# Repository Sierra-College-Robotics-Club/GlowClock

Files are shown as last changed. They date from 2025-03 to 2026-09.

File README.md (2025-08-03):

# GlowClock

This is a project from Sierra College Robotics Club, A glow-in-the-dark display, activated by UV LEDs scanning over a glow-in-the-dark surface. It displays messages, the time, and features various patterns and simple games! 

See [The Schematic](GlowClockPCB/Docs/GlowClockSchematicPrint.pdf) and [The Code](code/glowClock.py) to get started working with it.

The GlowClock design evolved from our previous project, the Whiteboard Clock, but with the goals of being more mechanically reliable, while showing a new and unique way of using technology we're all familar with: Glow in the dark materials!

The GlowClock is a collaborative effort by the Robotics Club, featuring PCB design and software by Patrick Leiser, with mechanical design and assembly contributions from many talented club members.

## In the media
We presented the GlowClock at OpenSauce 2025, and were featured in [This Video](https://youtu.be/PQWQQJ_izac?t=115) by Jeff Geerling. We also posted some media on [our instagram](https://www.instagram.com/p/DJci4YWBg5E/)

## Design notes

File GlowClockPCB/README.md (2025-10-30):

# GlowClock PCB
This PCB was designed to, in addition to supporting the glowclock, be a modular prototyping board for various other projects as well, with all unused GPIO broken out and accessible.

V1.0 boards have been produced and are in active use, V1.1 boards are currently under development.

## Errata
### V1.0
- The second motor-driver board slot (A2) is not fully populated with the required control signals
- The Raspberry Pi 40 pin header (not to be confused with the Pi Pico's socket) has 0.2mm hole spacing instead of the traditional 2.54mm spacing
- The i2c SDA pin for the I2C_LCD connector is connected to GPIO22 instead of GPIO20. This can be resolved by cutting the trace and green-wiring to the Pi Pico pin 26.

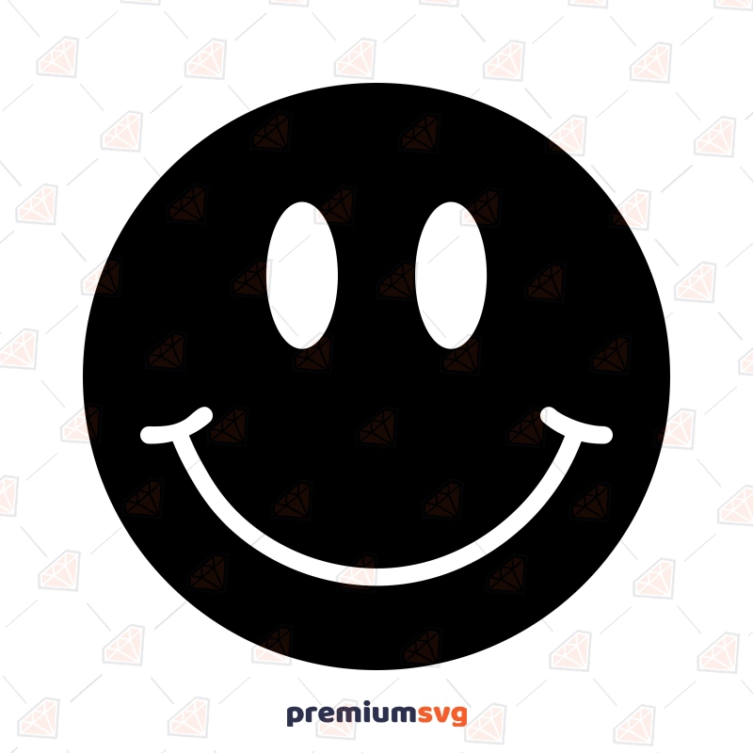
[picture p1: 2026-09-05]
code/images/smile-inv.webp

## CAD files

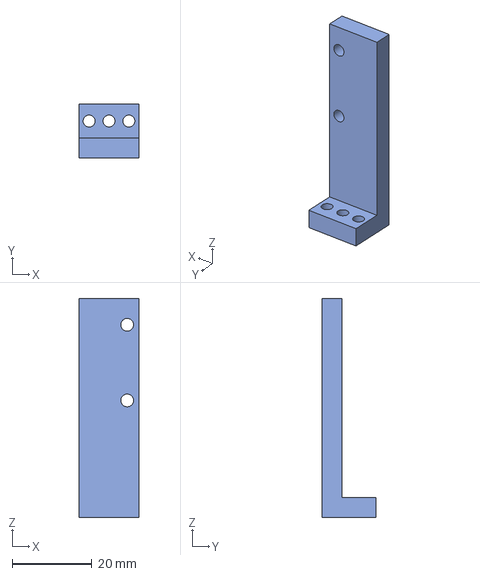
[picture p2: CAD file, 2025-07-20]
3d Models/GlowClockOriginSwitchBracket-2.step
15.0 x 13.5 x 55.0 mm

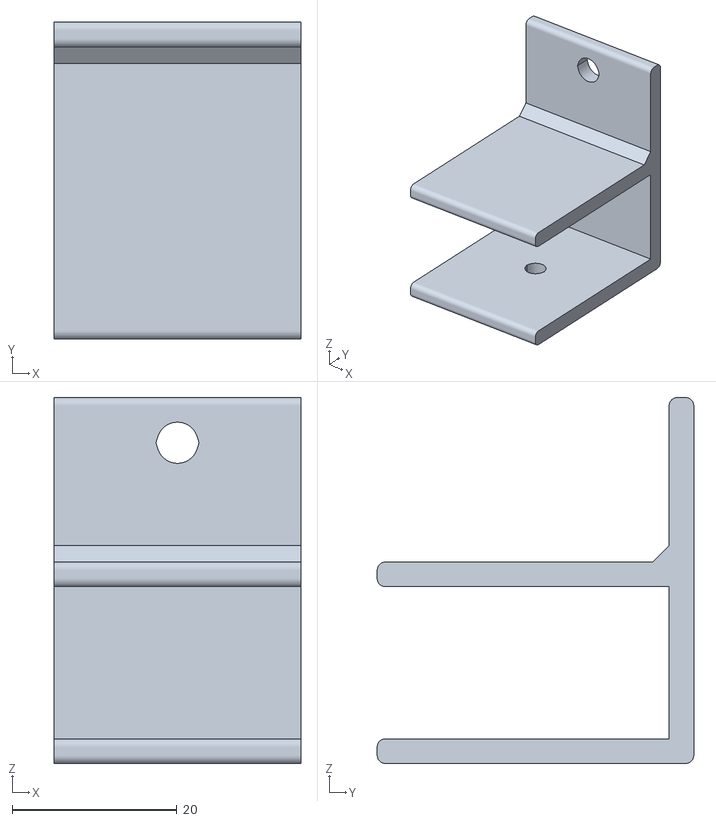
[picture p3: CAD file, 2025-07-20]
3d Models/GraphBot/GraphBotBracket.stl
30.0 x 38.5 x 44.5

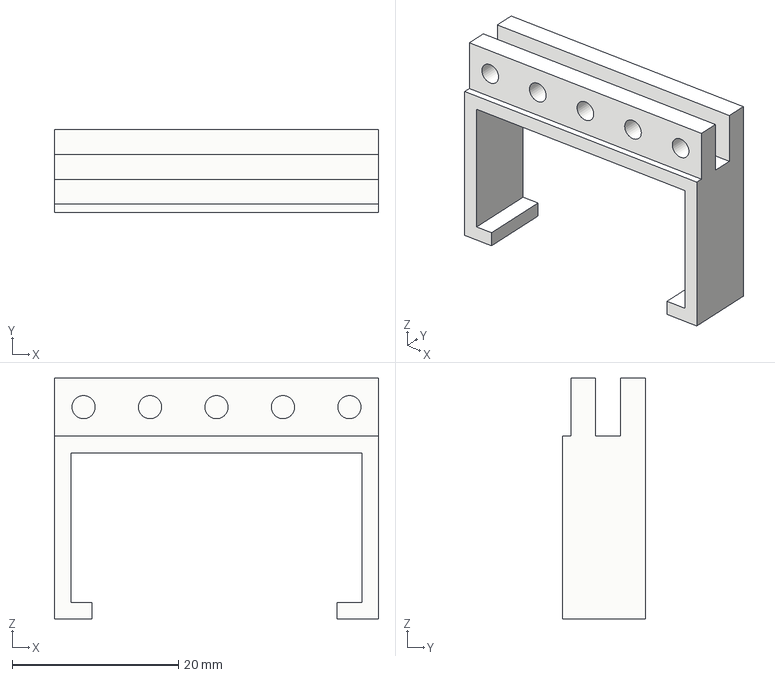
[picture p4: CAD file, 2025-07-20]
3d Models/Belt_Mesh_Joint v3.3mf
39.0 x 10.0 x 29.0 mm

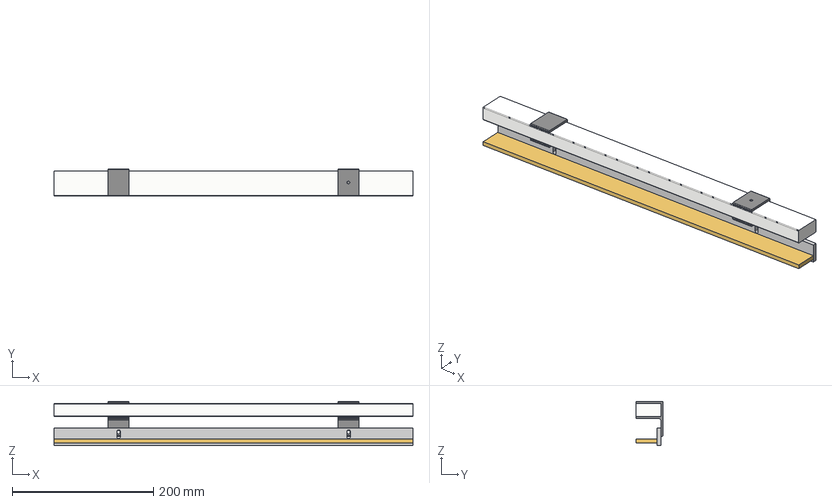
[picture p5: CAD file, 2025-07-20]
3d Models/GraphBot/GraphBotMount.step
508.2 x 38.5 x 62.9 mm
Mount
WoodBracket
LedStripHolder
Mount(Mirror)

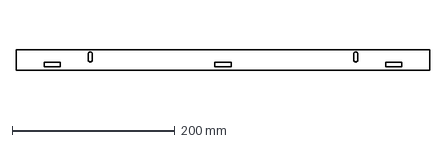
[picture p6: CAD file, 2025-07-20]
3d Models/GraphBot/WoodBracketCutout.dxf
508.0 x 25.0 mm

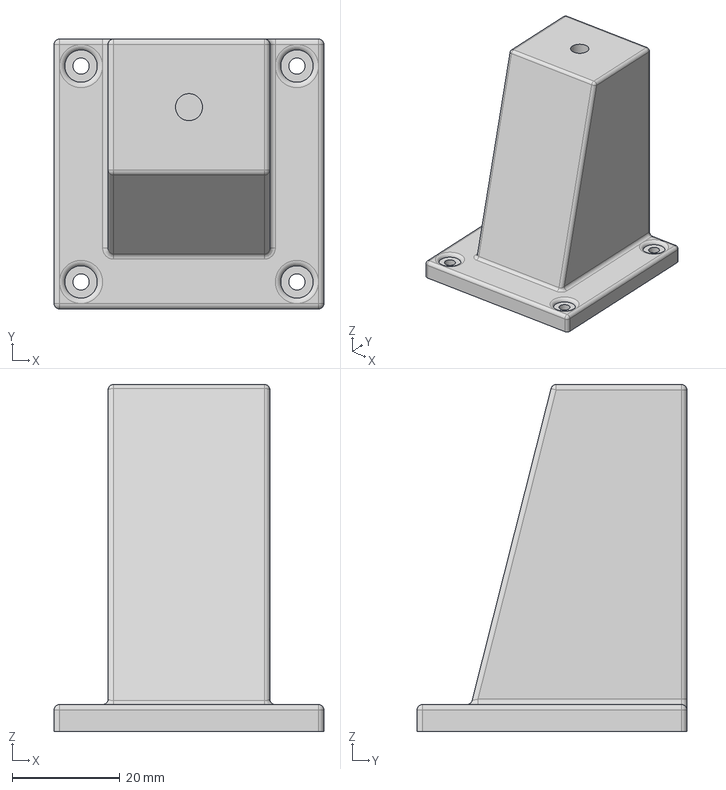
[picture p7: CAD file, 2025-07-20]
3d Models/GraphBot/MotorTensionMount v1.step
50.0 x 50.0 x 64.3 mm

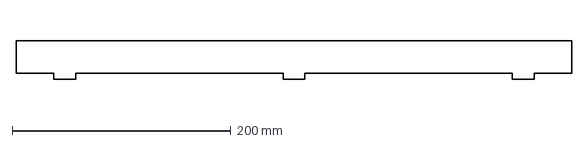
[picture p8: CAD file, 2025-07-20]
3d Models/GraphBot/LedMountCutout.dxf
508.0 x 35.5 mm

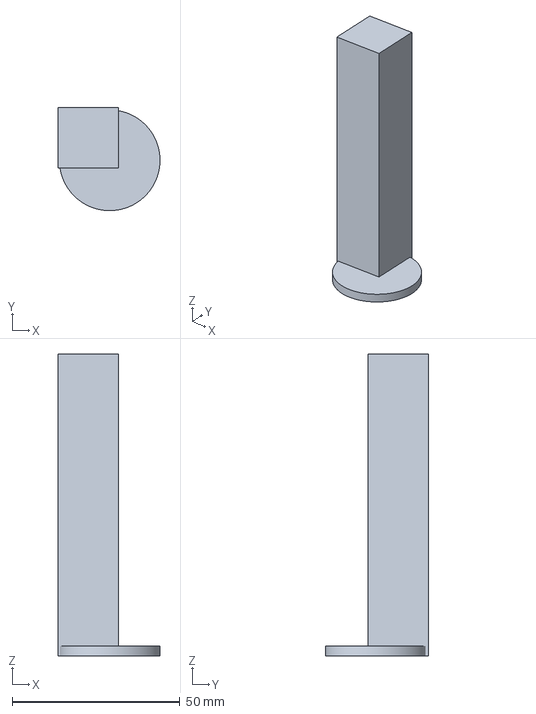
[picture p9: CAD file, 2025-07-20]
3d Models/shortenedactually3dprintableglowclockmount.3mf
30.4 x 30.8 x 90.0 mm

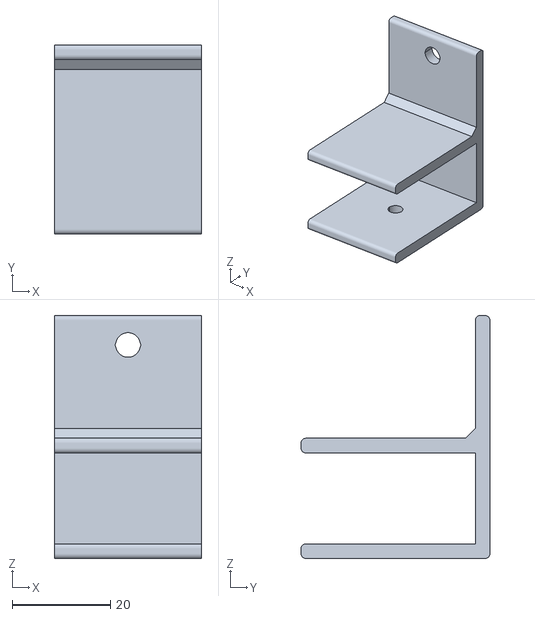
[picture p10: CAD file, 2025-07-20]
3d Models/GraphBot/MountFixv1.stl
30.0 x 38.5 x 49.5

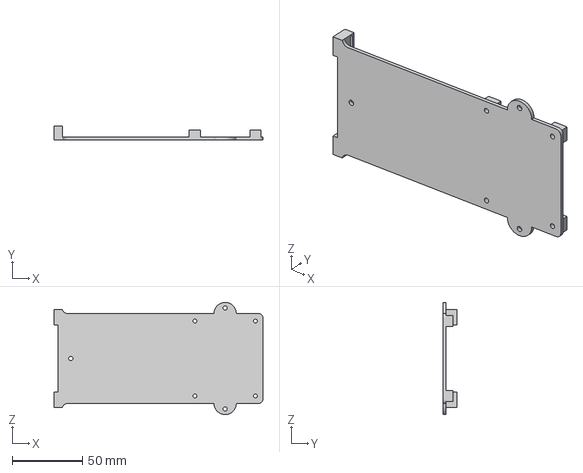
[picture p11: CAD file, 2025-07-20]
3d Models/glow clock pcb mount v2.3mf
149.0 x 10.0 x 80.0 mm

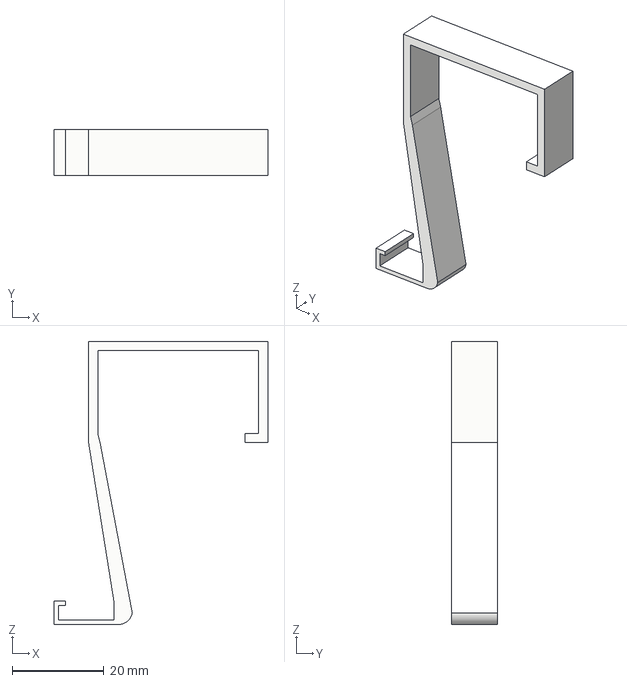
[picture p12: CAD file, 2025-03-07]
3d Models/LED_Strip_Hook v2.step
46.5 x 10.0 x 61.6 mm

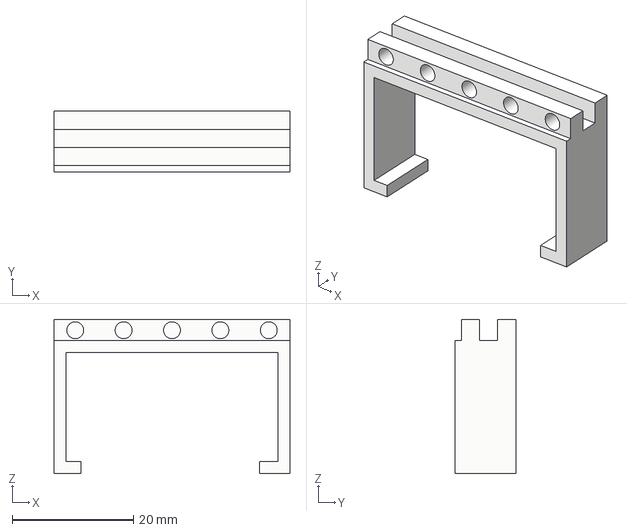
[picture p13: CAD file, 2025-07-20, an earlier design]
3d Models/Belt_Mesh_Joint v2.3mf
39.0 x 10.0 x 25.5 mm

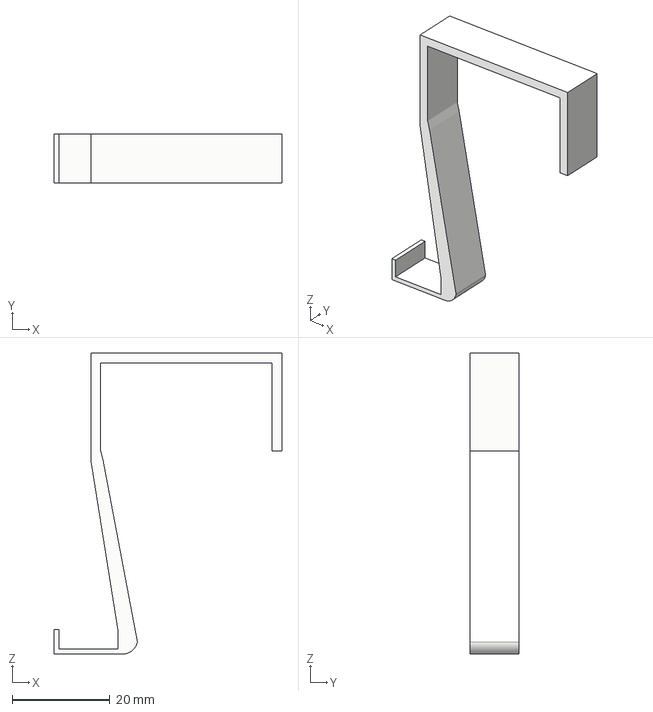
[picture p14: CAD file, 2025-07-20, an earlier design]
3d Models/LED_Strip_Hook v1.3mf
46.5 x 10.0 x 61.5 mm

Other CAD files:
3d Models/GlowClockOriginSwitchBracket.stl
3d Models/GraphBot/Motor Tension Moint.stl
3d Models/PowerSupplyCornerBracket.3mf
3d Models/LED_Strip_Hook v2.3mf
3d Models/PowerSupplyCornerBracket.stl

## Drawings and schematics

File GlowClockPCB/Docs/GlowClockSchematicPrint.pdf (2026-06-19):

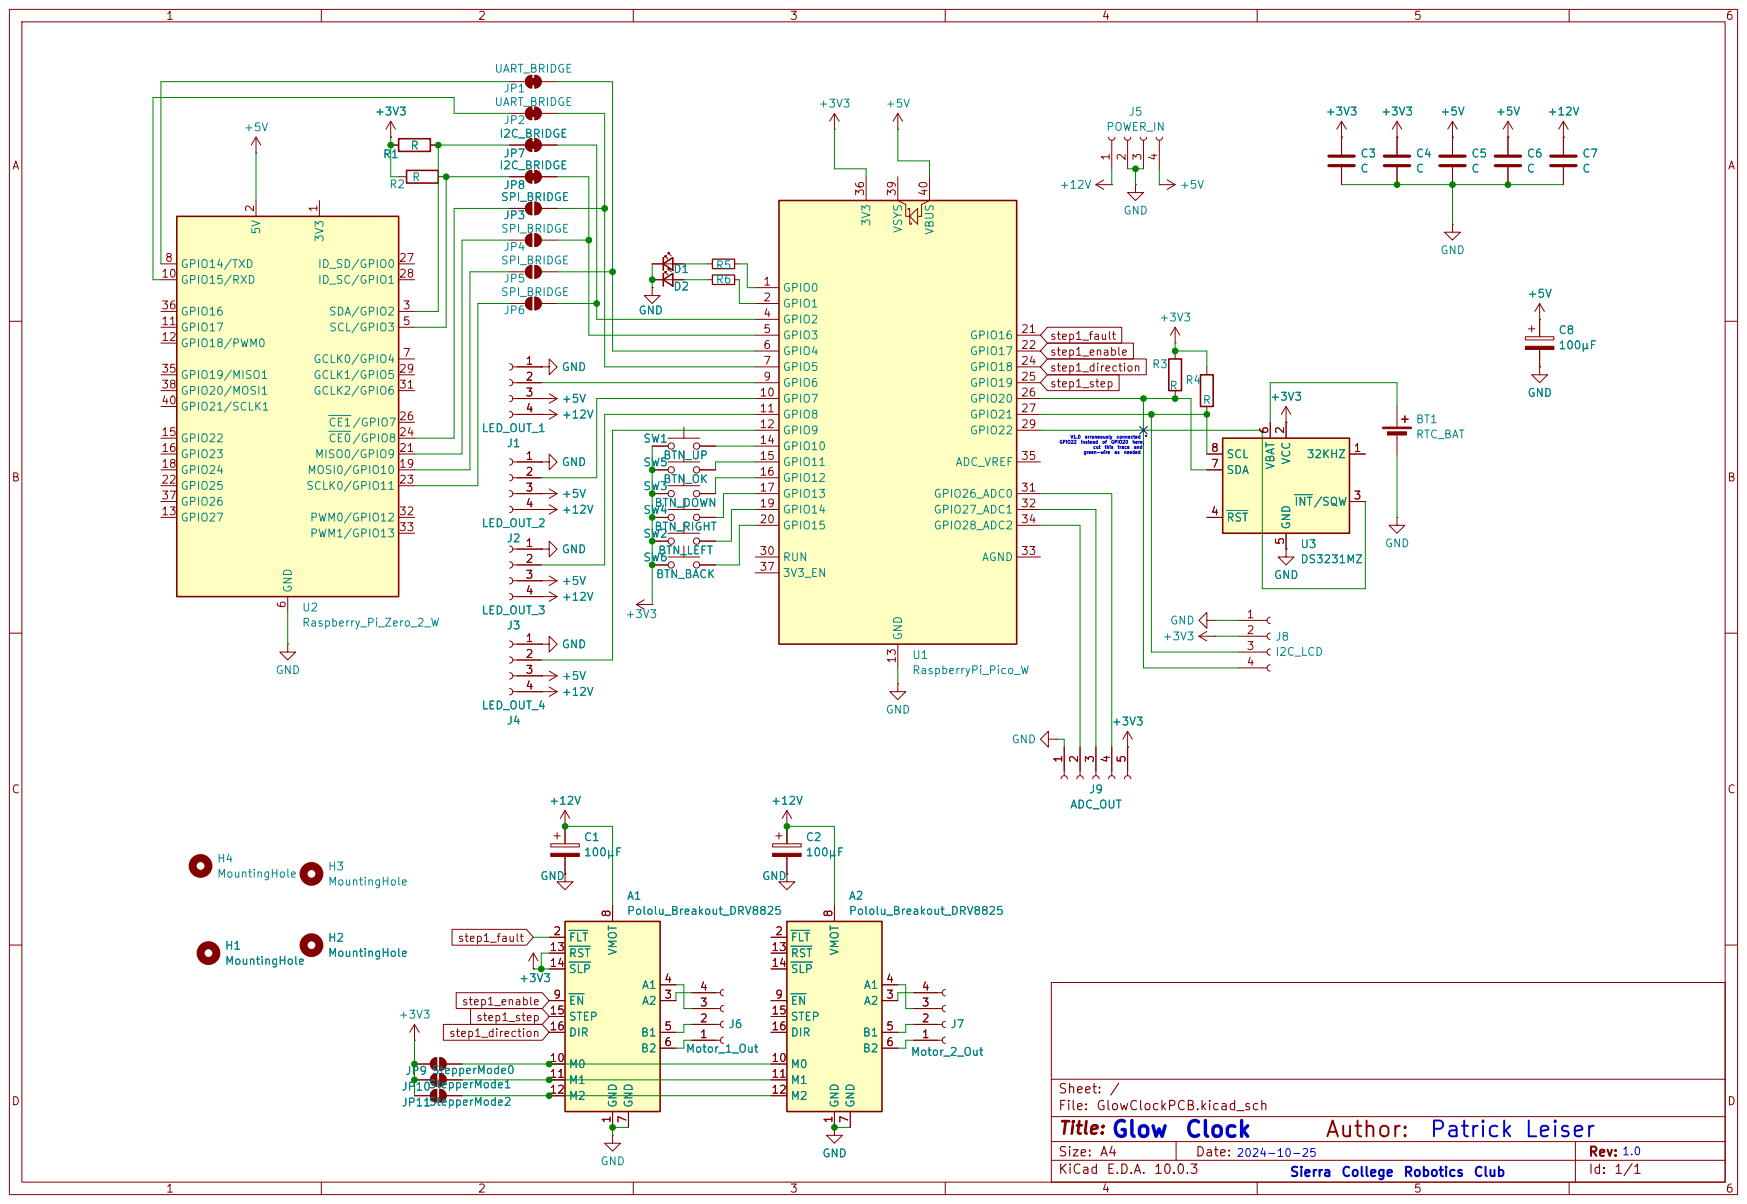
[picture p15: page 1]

Size: A4 | 2024-10-25 Sierra College Robotics Club | Rev: 1.0
KiCad E.D.A. 10.0.3 | | Id: 1/1

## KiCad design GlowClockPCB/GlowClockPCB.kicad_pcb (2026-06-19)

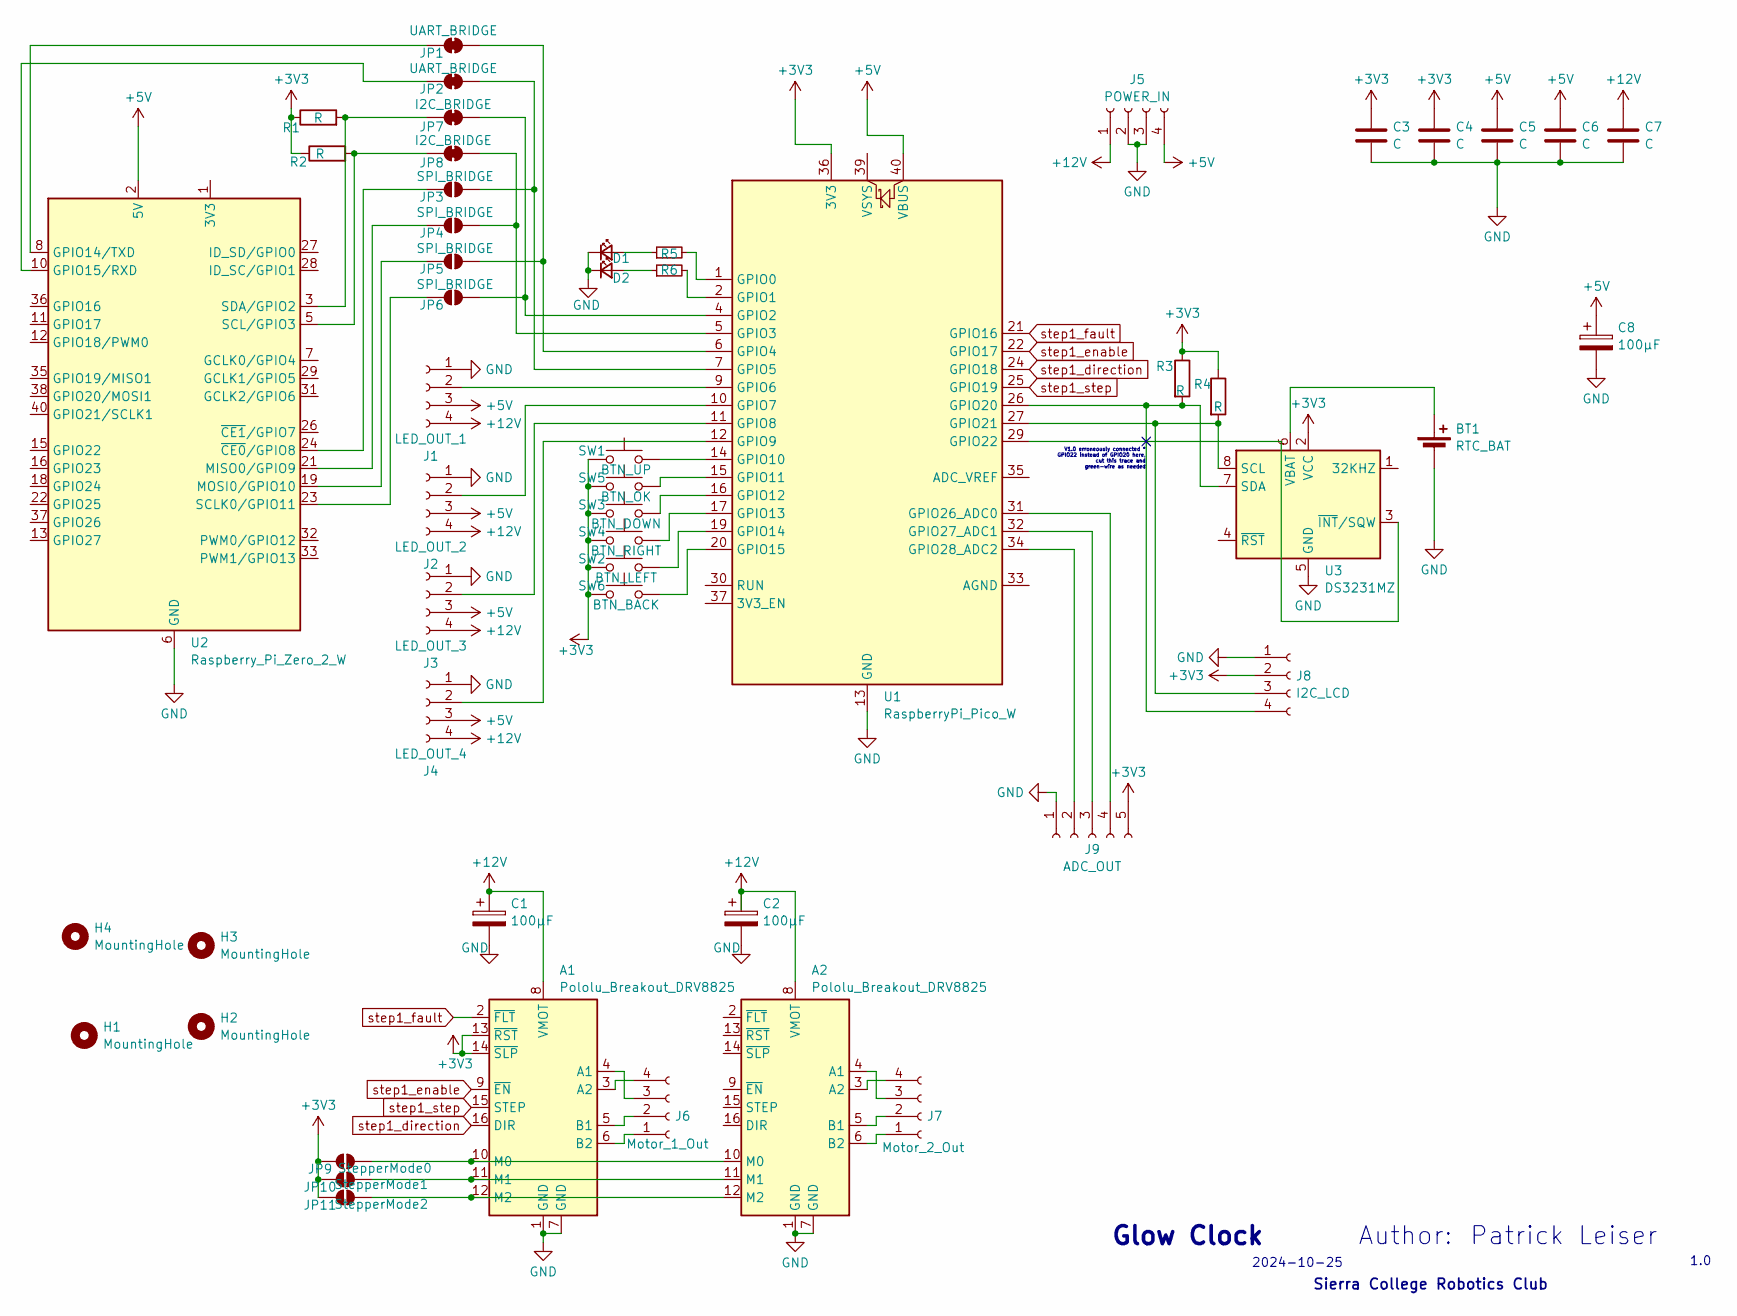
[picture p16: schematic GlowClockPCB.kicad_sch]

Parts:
A1, A2: Pololu_Breakout_DRV8825; Pololu_Breakout-16_15.2x20.3mm
BT1: RTC_BAT; BatteryHolder_LINX_BAT-HLD-012-SMT
C1, C2, C8: 100µF; CP_Radial_D10.0mm_P5.00mm
C3, C4, C5, C6, C7: C; C_0603_1608Metric
D1, D2: LED_Small; LED_0603_1608Metric
H1, H2, H3, H4: MountingHole; MountingHole_3.2mm_M3
J1: LED_OUT_1; JST_XH_B4B-XH-A_1x04_P2.50mm_Vertical
J2: LED_OUT_2; JST_XH_B4B-XH-A_1x04_P2.50mm_Vertical
J3: LED_OUT_3; JST_XH_B4B-XH-A_1x04_P2.50mm_Vertical
J4: LED_OUT_4; JST_XH_B4B-XH-A_1x04_P2.50mm_Vertical
J5: POWER_IN; TE_MATE-N-LOK_350211-1_1x04_P5.08mm_Vertical
J6: Motor_1_Out; JST_XH_B4B-XH-A_1x04_P2.50mm_Vertical
J7: Motor_2_Out; JST_XH_B4B-XH-A_1x04_P2.50mm_Vertical
J8: I2C_LCD; PinHeader_1x04_P2.54mm_Vertical
J9: ADC_OUT; JST_XH_B5B-XH-A_1x05_P2.50mm_Vertical
JP1, JP2: UART_BRIDGE; SolderJumper-2_P1.3mm_Bridged_Pad1.0x1.5mm
JP3, JP4, JP5, JP6: SPI_BRIDGE; SolderJumper-2_P1.3mm_Open_Pad1.0x1.5mm
JP7, JP8: I2C_BRIDGE; SolderJumper-2_P1.3mm_Bridged_Pad1.0x1.5mm
JP9: StepperMode0; SolderJumper-2_P1.3mm_Open_Pad1.0x1.5mm
JP10: StepperMode1; SolderJumper-2_P1.3mm_Open_Pad1.0x1.5mm
JP11: StepperMode2; SolderJumper-2_P1.3mm_Open_Pad1.0x1.5mm
R1, R2, R3, R4: R; R_0603_1608Metric
R5, R6: R_Small; R_0603_1608Metric
SW1: BTN_UP; SW_Push_1P1T_NO_6x6mm_H9.5mm
SW2: BTN_LEFT; SW_Push_1P1T_NO_6x6mm_H9.5mm
SW3: BTN_DOWN; SW_Push_1P1T_NO_6x6mm_H9.5mm
SW4: BTN_RIGHT; SW_Push_1P1T_NO_6x6mm_H9.5mm
SW5: BTN_OK; SW_Push_1P1T_NO_6x6mm_H9.5mm
SW6: BTN_BACK; SW_Push_1P1T_NO_6x6mm_H9.5mm
U1: RaspberryPi_Pico_W; RaspberryPi_Pico_Common
U2: Raspberry_Pi_Zero_2_W; PinHeader_2x20_P2.00mm_Vertical
U3: DS3231MZ; SOIC-8_3.9x4.9mm_P1.27mm

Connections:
+3V3: A1.13 (~RST), A1.14 (~SLP), C3.1, C4.1, J8.2, J9.5, JP9.1 (A), JP10.1 (A), JP11.1 (A), R1.1, R2.1, R3.1, R4.1, SW1.1, SW2.1, SW3.1, SW4.1, SW5.1, SW6.1, U1.36 (3V3), U3.2 (VCC)
+5V: C5.1, C6.1, C8.1, J1.3, J2.3, J3.3, J4.3, J5.4, U1.40 (VBUS), U2.2 (5V), U2.4 (5V)
+12V: A1.8 (VMOT), A2.8 (VMOT), C1.1, C2.1, C7.1, J1.4, J2.4, J3.4, J4.4, J5.1
GND: A1.1 (GND), A1.7 (GND), A2.1 (GND), A2.7 (GND), BT1.2 (-), C1.2, C2.2, C3.2, C4.2, C5.2, C6.2, C7.2, C8.2, D1.1 (K), D2.1 (K), J1.1, J2.1, J3.1, J4.1, J5.2, J5.3, J8.1, J9.1, U1.3 (GND), U1.8 (GND), U1.13 (GND), U1.18 (GND), U1.23 (GND), U1.28 (GND), U1.38 (GND), U2.6 (GND), U2.9 (GND), U2.14 (GND), U2.20 (GND), U2.25 (GND), U2.30 (GND), U2.34 (GND), U2.39 (GND), U3.5 (GND)
unnamed: A1.4 (A1), J6.3
unnamed: A1.3 (A2), J6.4
unnamed: A1.5 (B1), J6.2
unnamed: A1.6 (B2), J6.1
unnamed: A1.10 (M0), A2.10 (M0), JP9.2 (B)
unnamed: A1.11 (M1), A2.11 (M1), JP10.2 (B)
unnamed: A1.12 (M2), A2.12 (M2), JP11.2 (B)
unnamed: A2.4 (A1), J7.3
unnamed: A2.3 (A2), J7.4
unnamed: A2.5 (B1), J7.2
unnamed: A2.6 (B2), J7.1
unnamed: BT1.1 (+), U3.6 (VBAT)
unnamed: D1.2 (A), R5.1
unnamed: D2.2 (A), R6.1
unnamed: J1.2, U1.9 (GPIO6)
unnamed: J2.2, U1.10 (GPIO7)
unnamed: J3.2, U1.11 (GPIO8)
unnamed: J4.2, U1.12 (GPIO9)
unnamed: J8.3, R4.2, U1.27 (GPIO21), U3.8 (SCL)
unnamed: J8.4, R3.2, U1.26 (GPIO20), U3.7 (SDA)
unnamed: J9.2, U1.34 (GPIO28_ADC2)
unnamed: J9.3, U1.32 (GPIO27_ADC1)
unnamed: J9.4, U1.31 (GPIO26_ADC0)
unnamed: JP1.1 (A), U2.8 (GPIO14/TXD)
unnamed: JP1.2 (B), JP5.2 (B), U1.6 (GPIO4)
unnamed: JP2.1 (A), U2.10 (GPIO15/RXD)
unnamed: JP2.2 (B), JP3.2 (B), U1.7 (GPIO5)
unnamed: JP3.1 (A), U2.24 (~CE0/GPIO8)
unnamed: JP4.1 (A), U2.21 (MISO0/GPIO9)
unnamed: JP4.2 (B), JP8.2 (B), U1.5 (GPIO3)
unnamed: JP5.1 (A), U2.19 (MOSI0/GPIO10)
unnamed: JP6.1 (A), U2.23 (SCLK0/GPIO11)
unnamed: JP6.2 (B), JP7.2 (B), U1.4 (GPIO2)
unnamed: JP7.1 (A), R1.2, U2.3 (SDA/GPIO2)
unnamed: JP8.1 (A), R2.2, U2.5 (SCL/GPIO3)
unnamed: R5.2, U1.1 (GPIO0)
unnamed: R6.2, U1.2 (GPIO1)
unnamed: SW1.2, U1.14 (GPIO10)
unnamed: SW5.2, U1.15 (GPIO11)
unnamed: SW3.2, U1.16 (GPIO12)
unnamed: SW4.2, U1.17 (GPIO13)
unnamed: SW2.2, U1.19 (GPIO14)
unnamed: SW6.2, U1.20 (GPIO15)
unnamed: U1.29 (GPIO22), U3.3 (~INT/SQW)
unnamed: U2.1 (3V3), U2.17 (3V3)
step1_direction: A1.16 (DIR), U1.24 (GPIO18)
step1_enable: A1.9 (~EN), U1.22 (GPIO17)
step1_fault: A1.2 (~FLT), U1.21 (GPIO16)
step1_step: A1.15 (STEP), U1.25 (GPIO19)

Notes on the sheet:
1.0
Glow Clock
Author:
Patrick Leiser
Sierra College Robotics Club
V1.0 erroneously connected * GPIO22 instead of GPIO20 here, cut this trace and green-wire as needed
2024-10-25

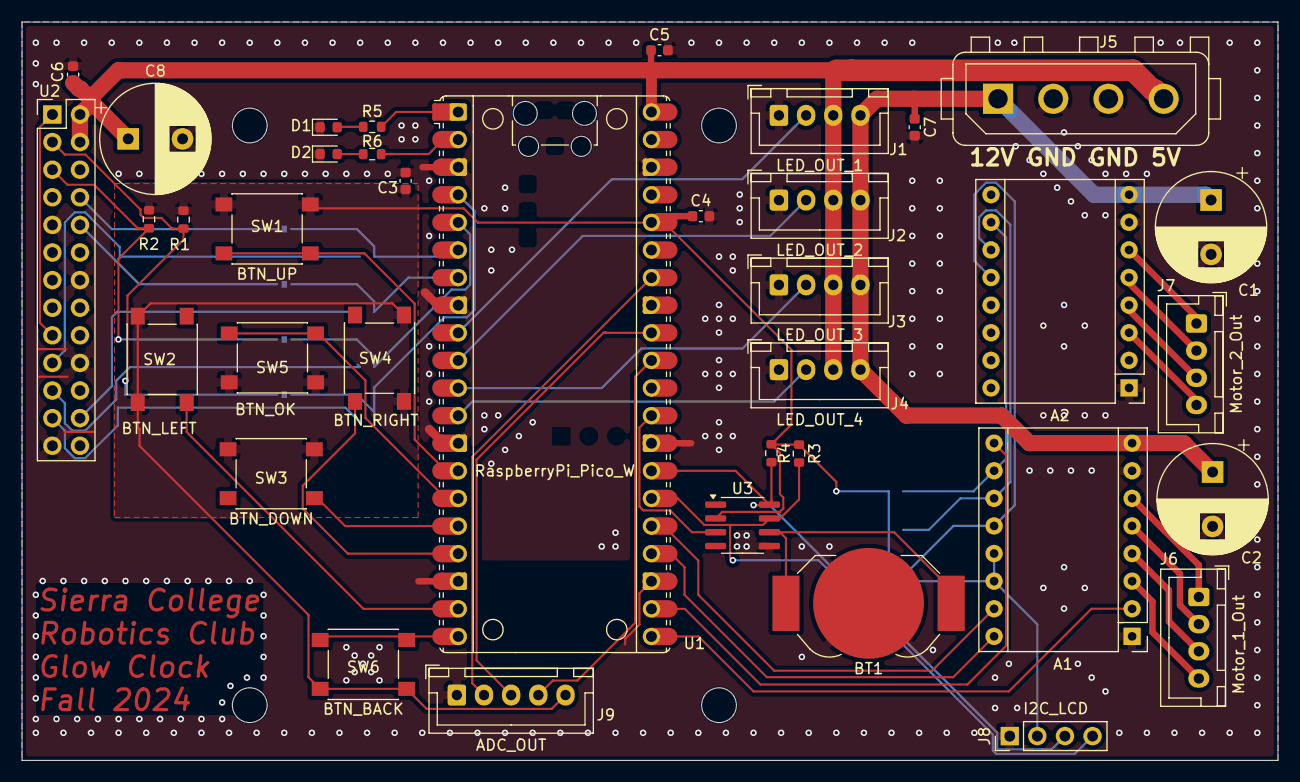
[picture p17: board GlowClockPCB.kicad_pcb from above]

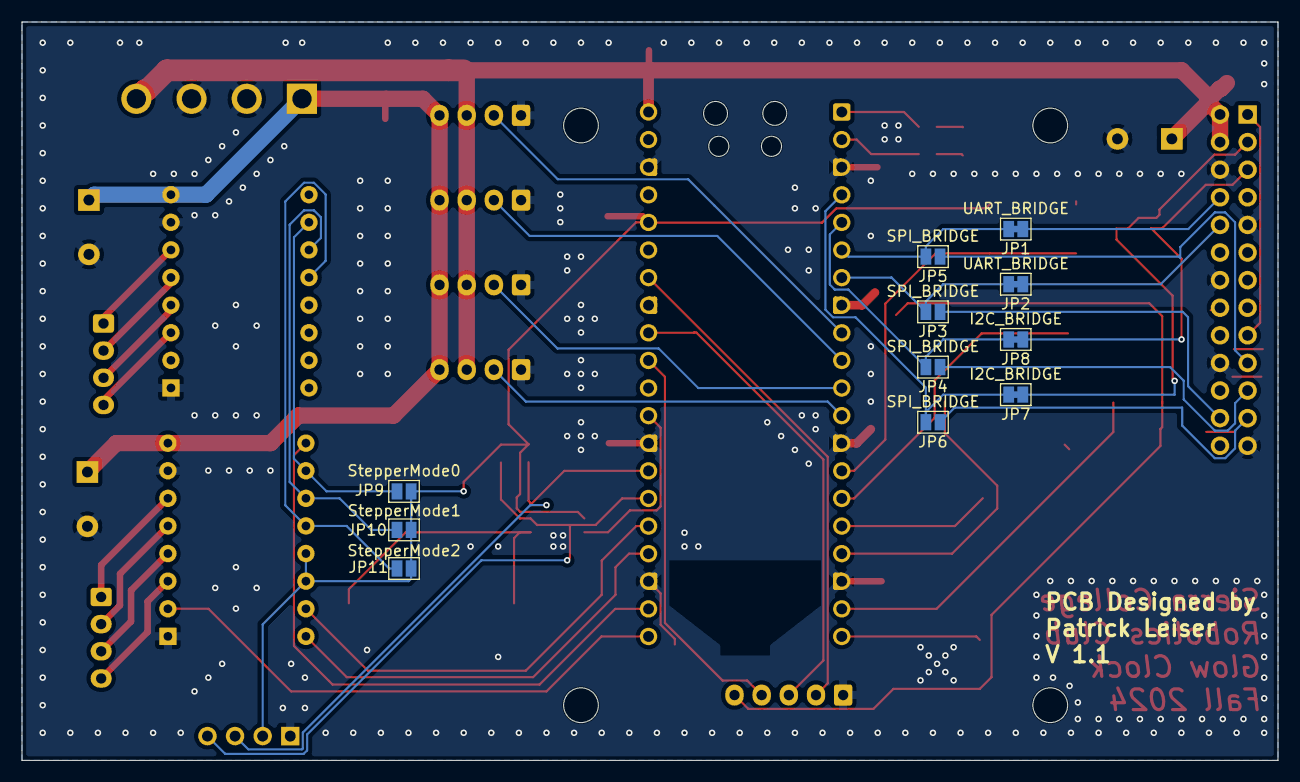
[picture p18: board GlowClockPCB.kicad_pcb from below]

Board: 2 copper layers, 115.6 x 67.9 mm, 52 parts (11 on the bottom side), 53 nets.

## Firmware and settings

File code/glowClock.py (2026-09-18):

# Main software for Sierra College Robotics Club Glow Clock
# designed by Patrick Leiser
# Tested with MicroPython 1.25
import time

import gc
import framebuf
import _thread
import random
import math
import array

from HAL import HARDWARE
from HAL import sdaPin, sclPin, i2c, ds, stepPin, dirPin, homeSensorPin
from HAL import okButtonPin, backButtonPin, upButtonPin, downButtonPin, leftButtonPin, rightButtonPin
from HAL import pixels, uv_pixels, uv_pixels2, num_pixels, num_uv_pixels

from image import img

updateEverySeconds = 60

microSecondsPerStep = 750

#print(pixels.brightness)
pixels.brightness = 0.45
pixels.auto_write = False
uv_pixels.brightness = 1.0
uv_pixels.auto_write = False


#constants: 
#dimensions of virtual and physical displays
travelSteps = 4250
stepsPerPixel = 32
bufW = int(travelSteps/stepsPerPixel)+1
bufH = 60

colorW = bufW
colorH = num_pixels

uvW = bufW
uvH = num_uv_pixels*2

pixelDepth = 2;
frameBuf_pixelDepth = framebuf.GS2_HMSB
maxColor = (2**pixelDepth)-1; #2 bits per pixel, values 0-3

pixelColorMap = [0, 20, 90, 255]

# Shared variables for multithreading
steps_needed = 0
step_direction = 0
step_lock = _thread.allocate_lock()

stepCounterForward = 0
stepCounterHomeSkipped = 0
stepCounterReverse = 0

lastUpdateTotalSeconds = 0

currentStage = 0

gameTargetRow = 0

isEraseCycle = False
specialModeGlobal = 0
hdRenderModeGlobal = 1

print(gc.mem_free())
#+4 prevents value error, TODO figure out cause of that (allocation slightly too small)
fbuf = framebuf.FrameBuffer(bytearray(round((bufW+8)*(bufH)/4)), bufW+4, bufH, frameBuf_pixelDepth)

print(gc.mem_free())
#optional, for double-buffered frames
#fbuf2 = adafruit_framebuf.FrameBuffer(bytearray(round(bufW*bufH/4)), bufW, bufH, adafruit_framebuf.GS2_HMSB)
#print(gc.mem_free())

#    fbuf.pixel(x, y, color)

#each message can be up to 3 rows of 16 characters, or 2 rows and time
    #"1234567890123456","1234567890123456" , "1234567890123456"
messageArray = [

   #  ["Sierra College",  "Robotics Club!" ],
#    ["Hello", "San Francisco!", "Welcome To", "Open Sauce 2026!"],
#    ["Welcome To",      "Maker Faire!"],
#    ["Special Action", "Dots"],
  #   ["Please don't",    "Touch! I'm busy"],
#    ["Hello World",     "This is a TEST" ],
#     ["Special Action", "Game4"],
#    ["Howre you doing", "Because I'm a",     "Glow Clock!"],
    #["In your world",   "with human time"],

    #["ALL YOUR BASE",   "ARE BELONG TO US"],

   #  ["Special Action", "Polygons"],
    #["follow us on",  "instagram", "@sierrabeepbop"],
#    ["Special Action", "Gradient"],
    #["welcome to the",  "makerspace!"],
#    ["Narnian time:",   "Synchronized"],
 #    ["UV + Glow Paint", "=Glow Clock!"],
    # ["Special Action", "CursedPolygons"],
     ["Special Action", "Image"],
     #["Special Action", "Image", "smile.py"], #WIP implementation
#    ["Special Action", "Gradient2"],
#    ["Special Action", "Draw Square"],
#    ["this is a long", "message, please","do not read it", "or you will know"],
#    ["I like shiny", "things. Do you?"]
    


]


def scanI2C():
    devices = i2c.scan()
    if len(devices) != 0:
        print('Number of I2C devices found=',len(devices))
        for device in devices:
            print("Device Hexadecimel Address= ",hex(device))
    else:
        print("No i2c devices found")

#update to desired values, only call when intially setting clock
def setRTCTime():
    now = ds.datetime()
    print(f"setting time from {now}")
    year = 2026 # Can be yyyy or yy format
    month = 4
    mday = 28
    hour = 16 # 24 hour format only
    minute = 17
    second = 0 # Optional
    weekday = 3 # Optional, Sunday = 1
    datetime = (year, month, mday, hour, minute, second, weekday)
    ds.datetime(datetime)
    now = ds.datetime()
    print(f"setting time to {now}")



def profileTiming(label, start_ms, end_ms):
    elapsed_ms = time.ticks_diff(end_ms, start_ms) / 1000  # convert to microseconds
    print(f"{label}: {elapsed_ms:.1f} ms")

def setPixelColumn(pixelString, width, height, colX, step=1, start=0):
    
    #scale = 255 / maxColor
    for i, y in enumerate(range(start, height-step+1, step)):
        #print("x: ",colX,"  y:",y)
        pixelVal = fbuf.pixel(colX, y)
        val = pixelColorMap[pixelVal] # 255 - () for inverted mode
        pixelString[i] = (val, val, val)

def setHDpixelColumn(pixelString1, pixelString2, width, height, baseColX):
    setPixelColumn(uv_pixels, uvW, uvH+1, baseColX+2, 2,1)
    setPixelColumn(uv_pixels2, uvW, uvH, baseColX, 2,0)
    
def simPixelsWrite(frameBuf, column, height):
    for i in range(0, height-1):
        if(frameBuf.pixel(column, i)):
            print("█", end="")
        else:
            print(" ", end="")
    print("")

def homeRoutine():
    for i in range (1, (bufW*4)+10):
        uv_pixels[ i % num_uv_pixels ] = (255, 255, 255)
        uv_pixels[ (i-1) % num_uv_pixels ] = (0,0,0)
        uv_pixels2[ i % num_uv_pixels ] = (255, 255, 255)
        uv_pixels2[ (i-1) % num_uv_pixels ] = (0,0,0)
        uv_pixels.write()
        uv_pixels2.write()
        #waitForSteps()
        requestMotion(stepsPerPixel/4, 1)
    requestMotion(stepsPerPixel*2, 0) #back off one step
    waitForSteps()


def clearDisplay():
    fillDisplay(0)

def fillDisplay(newColor):
    fbuf.fill(newColor)
    #fbuf.rect(0,0,bufW,bufH-2,newColor)


def renderLogo():
    fbuf.text("Sierra College",2,1,maxColor)
    fbuf.text("Robotics Club!",2,10,maxColor)
    renderTime(19)
    renderDate(29)
    renderWeekday(39)
    #fbuf.text("Hi",2,18,maxColor)
    
def renderText(text, x, y, color):
    fbuf.text(text, x, y, color)

def renderTime(heightOffset):  #note 19 is good offset for 3rd row alignment
    (year, month, day, weekday, hour, minute, second, zero) = ds.datetime()
    print(f"it is {hour}:{minute}")
    #fbuf.fill(1)
    #erase the time field
    minuteSpacer = ""
    fbuf.rect(0,heightOffset, bufW, 11, 0, True)
    if hour > 12:
        hour = hour - 12
    if minute < 10:
        minuteSpacer="0"
    fbuf.text(f"it is {hour}:{minuteSpacer}{minute}",2,heightOffset+1,maxColor)
    drawPolygon((int(second/6)%10)+1, 110, heightOffset+4,  7,  maxColor)

def renderDate(heightOffset):
    (year, month, day, weekday, hour, minute, second, zero) = ds.datetime()
    monthArr = ["NaM","Jan", "Feb", "Mar", "Apr", "May", "Jun", "Jul", "Aug", "Sep", "Oct", "Nov", "Dec"]
    daySuffixArr = ["th","st", "nd", "rd", "th", "th", "th", "th", "th", "th", "th"]
    print(f"on {monthArr[month]} {day}{daySuffixArr[day%10]}, {year}")
    fbuf.text(f"{monthArr[month]} {day}{daySuffixArr[day%10]}, {year}",2,heightOffset+1,maxColor)

def renderWeekday(heightOffset, length=10):
    (year, month, day, weekday, hour, minute, second, zero) = ds.datetime()
    dayArr = ["NaD","Sunday", "Monday", "Tuesday", "Wednesday", "Thursday", "Friday", "Saturday"]
    print(f"happy {dayArr[weekday]}")
    fbuf.text(f"happy {dayArr[weekday][0:length]}",2,heightOffset+1,maxColor)
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

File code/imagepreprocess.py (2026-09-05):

import os
from PIL import Image
import numpy as np

pixelAspectRatio = 1.25
maxSize = (130/pixelAspectRatio, 60)
maxW, maxH = maxSize

im = Image.open(os.path.dirname(os.path.abspath(__file__))+'/images/smile-inv.webp').convert('L')
print ("input image:",im.format, im.size, im.mode)
(inW, inH) = im.size

scale = min(maxW/inW, maxH/inH)
#print(scale)

newW = int(inW*scale*pixelAspectRatio)
newH = int(inH*scale)
print("output dimensions:",(newW, newH))
#im.thumbnail(maxSize)
im = im.resize((newW, newH))
im.save(os.path.dirname(os.path.abspath(__file__))+"/images/small.jpg", "JPEG") #save sample image (8 bit greyscale)
print("8-bit preview saved to /images/small.jpg")
#im.show()
arr = np.asarray(im) >> 6  # convert to 2 bit greyscale that the glowclock framebuffer uses

np.set_printoptions(threshold=np.inf)
#print(np.array2string(arr, separator=', '))

with open (os.path.dirname(os.path.abspath(__file__))+'/lib/image.py','w', encoding='utf-8') as f:
	f.write("img = "+np.array2string(arr, separator=', ')) 

print("image saved to /lib/image.py")
print("copy image.py to glowclock's filesystem to use")

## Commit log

2024-09-19 initial commit, most of basic layout and schematic complete
    [GlowClockPCB.kicad_pcb, GlowClockPCB.kicad_sch]
2024-09-19 add output connectors for motor drivers
    [GlowClockPCB.kicad_pcb, GlowClockPCB.kicad_sch]
2024-09-19 thicken high-current traces, and move text from silkscreen to copper layer
    [GlowClockPCB.kicad_pcb]
2024-10-02 lots of tweaks to design, add display port, mounting holes, decoupling caps, etc
    [GlowClockPCB.kicad_pcb, GlowClockPCB.kicad_sch]
2024-10-02 tweaks to resolve DRC errors
    [GlowClockPCB.kicad_pcb, GlowClockPCB.kicad_sch]
2024-10-25 finalize design for export, add schematic to docs
    [GlowClockPCB.kicad_pcb, GlowClockPCB.kicad_sch]
2024-11-28 simple test of stepper motor, works great
2025-03-07 glowClock.py sucessfully writes messages when manually pushed
    [LED_Strip_Hook v2.step]
2025-04-12 reimplement setPixelColumn to cut delay in half, add timing to track delays, and remove debug logs that added significant delays
2025-04-18 initial implementation switching from circuitPython to MicroPython
2025-04-25 log skipped steps, lower movement speed to improve reliability, and remove magic number for step timing
    [glowClock.py]
2025-07-10 fix time formatting, add progress bar for sub-minute time indication, add row of usable pixels, add special functions (dots and game)
    [glowClock.py]
2025-07-20 add a bunch of 3D models
    [Belt_Mesh_Joint v2.3mf, Belt_Mesh_Joint v3.3mf, GlowClockOriginSwitchBracket-2.step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]
2025-08-02 first pass at 2nd led strip handling, attempts to offset other row by 1 pixel for text, non-framebuf displays WIP
2025-08-03 Document pin layout in comments at start of glowClock.py
2025-09-14 first pass at adding Hardware Abstraction Layer (HAL) allowing simulation. Simulate Realtime clock to allow existing program to run. Next step is to simulate printing with framebuffer
2025-09-18 Fixed Broken stuff and added Rhombus
    [glowClock.py]
2025-10-23 fix progressbar and stuck pixel
    [glowClock.py]
2025-10-30 Create README.md for the PCB directory, with V1.0 Errata
2025-10-30 fix time display alignment with longer messages
    [glowClock.py]
2025-10-30 correct SDA connection for I2C_LCD port
    [GlowClockPCB.kicad_pcb, GlowClockPCB.kicad_sch]
2025-10-30 Replace 40 pin 2.0mm header with 26 pin 2.54mm header
    [GlowClockPCB.kicad_pcb]
2026-02-10 pcb updates
    [GlowClockPCB.kicad_pcb]
2026-02-11 fix button brightness and bypass stuck up-button
    [glowClock.py]
2026-02-27 implement simulator's ability to print the pixels, just uncomment #HARDWARE = 'PICO_SIM' in HAL.py
2026-04-28 Update PCB to Kicad 10
    [GlowClockPCB.kicad_pcb, GlowClockPCB.kicad_sch]
2026-06-19 update schematic to annotate v1 pcb errata, add ibom and svg schematic
    [GlowClockPCB.kicad_pcb, GlowClockPCB.kicad_sch]
2026-06-21 update stepperTest.py from circuitpython to micropython
